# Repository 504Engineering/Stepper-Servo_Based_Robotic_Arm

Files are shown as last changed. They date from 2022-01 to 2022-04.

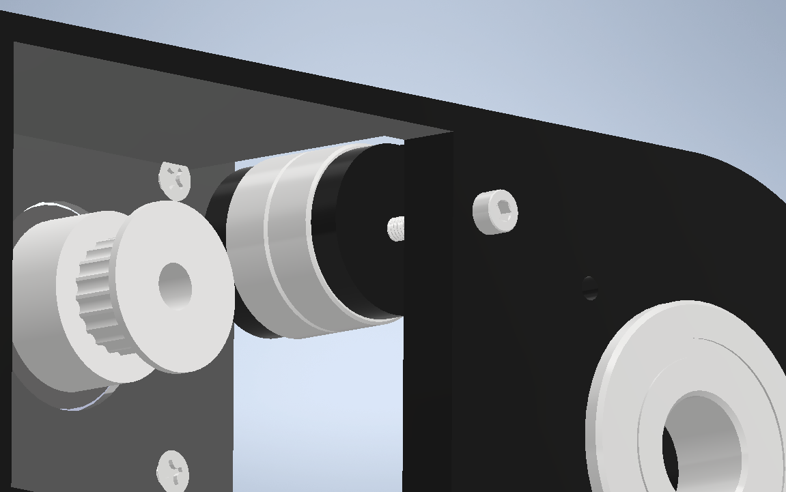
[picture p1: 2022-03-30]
Documentation/imgs/assembly6.png

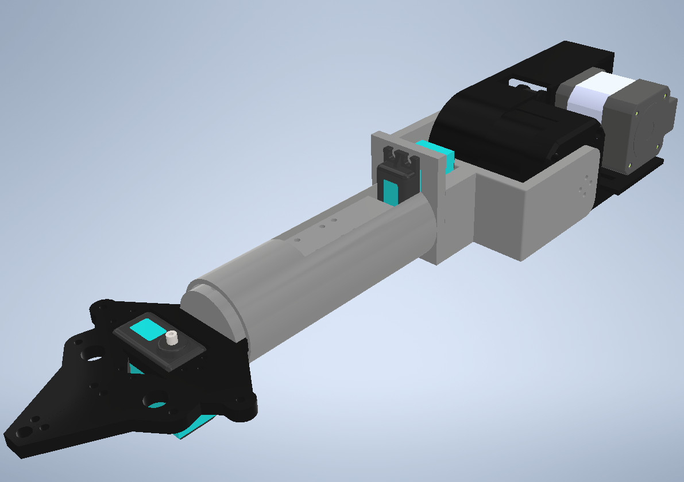
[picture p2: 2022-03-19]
Documentation/imgs/Full_Design.bmp

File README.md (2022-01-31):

# Stepper-Servo_Based_Robotic_Arm
This repository contains a robotic arm that is either a hybrid of both Servo Motors and Stepper Motors or just Stepper Motors.

Eventual completed arm will contain either four Stepper Motors or 2 Stepper Motors and 2 Servo Motors depending on which one you go with. All parts can be 3d printed and a few of the parts can be made on a cnc for quicker creation. 

At the current stage of development, the first two stages of the robotic arm's tilt are complete. 



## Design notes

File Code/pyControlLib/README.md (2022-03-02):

This Library is for use with 504 Engineering Robotic Arm. 

It is used to send signals and data to a RPI pico via a serial communication link.

Libraries that are installed with it:
    pySerial
    Numpy

This library contains useful functions that can be used to accurately store and send data to any serial device,
as long as the com port and baud rate are set correctly.

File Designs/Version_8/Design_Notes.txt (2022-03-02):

Tilt_attachment_Bracket:
	Minimum Distance in Length	97.376 mm
	Minimum Distance in Width	60 mm
	Minimim Distance in Height 	30 mm

Joint 1:
	110 mm length of gearbox = 4.331"
	Length of entire joint = 6"
	Extrusion Length = (6" - 4.331") * 25.4

	66m - 52mm = 14mm

Joint 2:
	40mm - 30mm = 10mm

twist:
	Length of rod = 65mm
	First d cut = 4 mm
	Second d cut = 65mm - 54.8mm - 4mm = 6.2mm

Claw Attachment:
	Length = 38.2mm
	Radius = max 37.5mm
	38.2 - 7e

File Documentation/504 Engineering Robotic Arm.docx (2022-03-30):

504 Engineering Robotic Arm

Documentation

By: Michael Lees

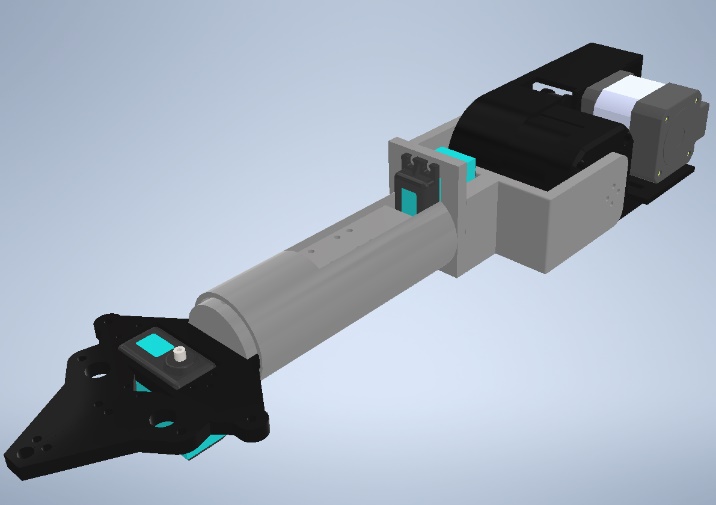
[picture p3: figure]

Table Of Contents:

- Chapter 1: Design Implementation …………………………………………………… 2
- Chapter 2: Gearbox Design …………………………………………………………... 5

Chapter 1: Design Implementation

504 Engineering’s stepper motor-based manipulator provides agile and precise movement across the ROV’s z axis. It utilizes a NEMA 17, provided by Doehler USA, which proved to be a challenge. This challenge was presented to us by North Paulding Robotics in order to achieve another first place victory in the MATE International Competition.

In December of 2021, they began the request with:

- 4-axes of movement
- At least two stepper motors in use (three if time allows)
- No servo motors in use.

They later changed the requirements, in March of 2022, to:

- 3-axes of movement
- Two stepper motors in use
- Ability to use one or two servo motors

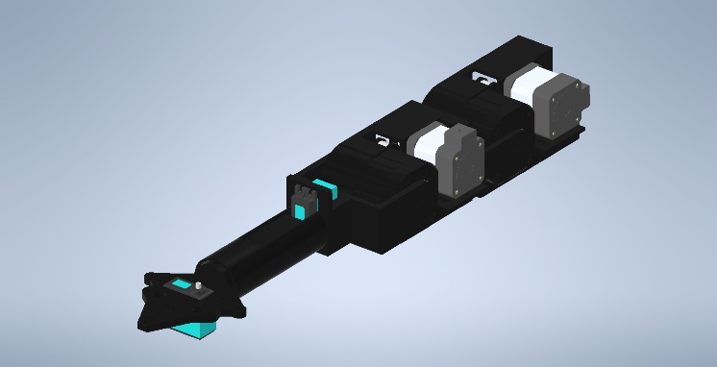
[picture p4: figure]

504 Engineering’s first design utilized four stepper motors to achieve the first set of requirements, however when inspected by North Paulding Robotics this design was determined to be an over improvement of the previous year’s design, in response a second set of requirements was given to us.

After a time period of two weeks a second design was presented, depicted in the image to the right. This design forgoes the second axis of tilt in favor of ease of use for the pilots who will not achieve the nominal amount of piloting time of the final ROV. The total time of completion of this project was four and a half months.

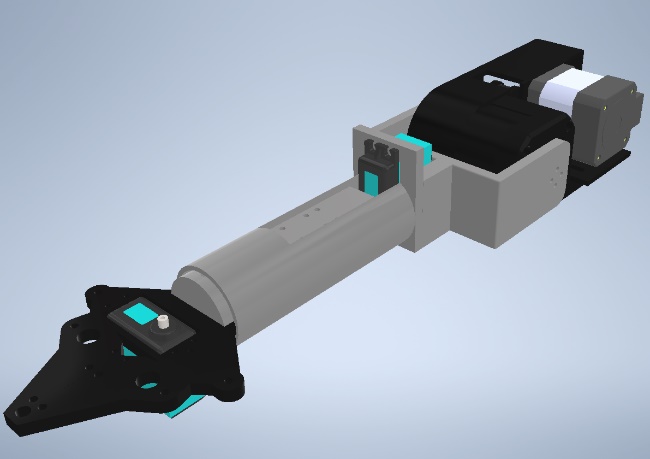
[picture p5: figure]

Chapter 2: Gearboxes

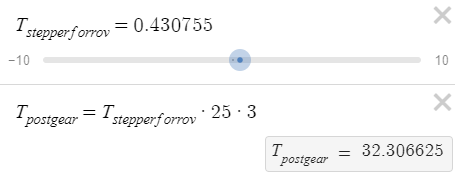
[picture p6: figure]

504 Engineering’s manipulator contains a NEMA 17 stepper motor with a holding torque capacity of 0.43 Newton-meter. This holding torque capacity, during initial testing, was determined to be inadequate for North Paulding Robotics needs. Testing proved that the utilization of a speed reducer gearbox provided the needed results to prove useful. With the utilization of a v-belt system (gear ratio of 3:1) along with the dual speed reduction gearbox, which was a 25:1 gear ratio, the holding torque of the NEMA 17 was increased to 32.31 Newton-meters.

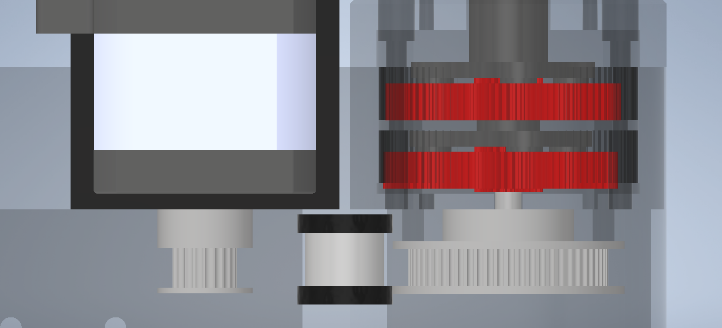
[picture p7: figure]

This combination of the v-belt system (the silver portions of the picture below) and the speed reduction gearbox (red portions) allowed for a 75:1 gear reduction of the NEMA 17. While this improved the overall torque capacity of the motor, it lessened the speed of the overall tilt. However, after research into the team’s previous manipulator designs it was shown that the angular speed of the tilt body was only slightly slower than the servo-based design used previously. Further research into the newly designed manipulator showed that the overall lifting capacity of the newly designed tilt was 9.08 kilograms at the overall length of the manipulator.

As you can see to the right, at the distance of 0.3 meter, the newly designed manipulator achieves a lifting force of 120.02 Newtons and a weight capacity of 12.25 kilograms. Included in the image is the calculations performed with the stepper motor without any gear reductions or v-belt systems, it can only achieve a lifting force of 1.6 Newtons and a weight capacity of 0.163 kilograms.

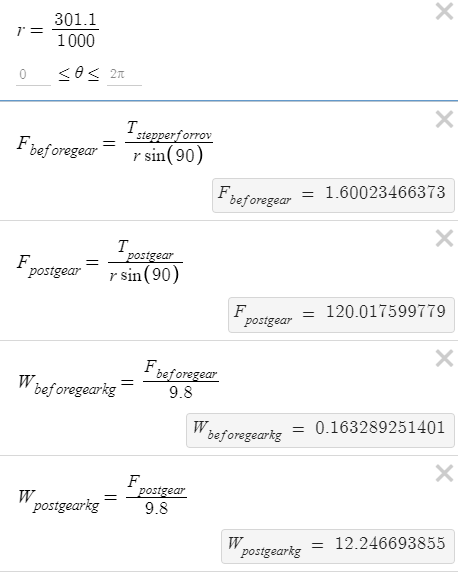
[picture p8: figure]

During the testing phases of the development of this gearbox reduction system, 504 Engineering tested various other options as well. Such as a cycloidal drive system, a harmonic drive system, stand-alone speed reduction gearboxes, and stand-alone v-belt systems. None of the listed options provided the nominal weight capacity required for the MATE International Competition as listed in their Product Demonstration Manual.

Chapter 3:

Part codex | Location in Parts Box | Description | Image

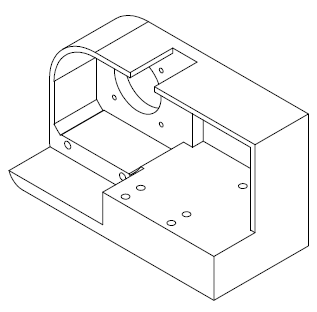
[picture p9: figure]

A0000 | | The base of tilt system

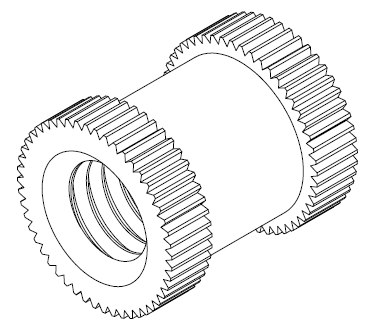
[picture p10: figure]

A0001 | | Threaded inserts

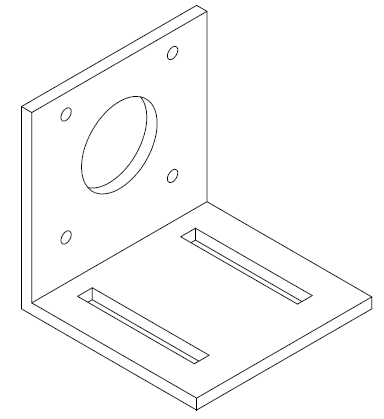
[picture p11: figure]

A0002 | | Black mount plate provided in the spare parts toolbox.

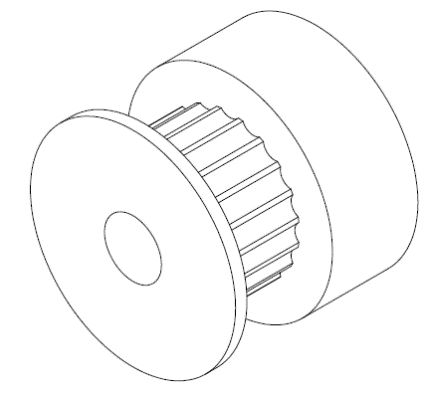
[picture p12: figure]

A0003 | | GT2 20 Tooth Drive Pulley
A0004 | | NEMA 17 Part number: STP-MTR-17040W Provided by: Doehler USA
A0005 | | Tension Bearing Holder Part 1

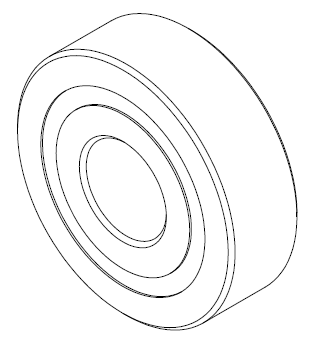
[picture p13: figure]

A0006 | | Tension Bearing, 626-2RS
A0007 | | Tension Bearing Holder Part 2

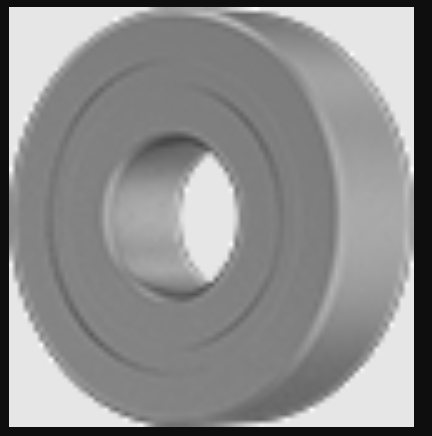
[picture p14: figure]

A0008 | | Side of Tilt Bearing 6021-2Z

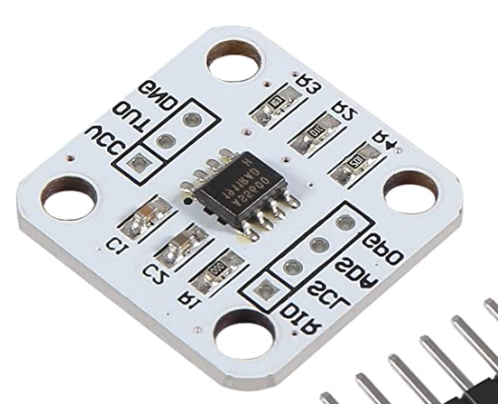
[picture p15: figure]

A0009 | | Magnetic Encoder

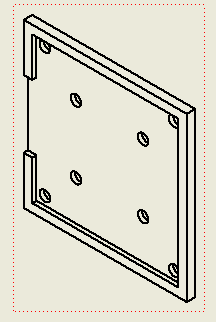
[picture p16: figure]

A0010 | | Magnetic Encoder Mounting Plate

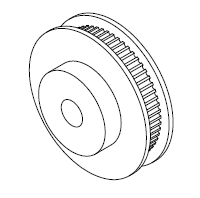
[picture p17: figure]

A0011 | | GT2 60 Tooth Belt Pulley
A0012 | | 5 mm x 30mm Aluminum Rod with a D slotted end

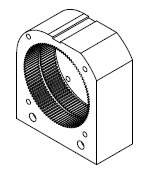
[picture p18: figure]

A0013 | | Speed Reducing Gear Box Casing
A0014 | | Sun Gear

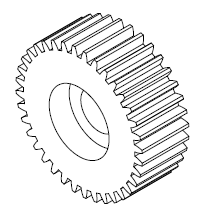
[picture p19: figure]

A0015 | | Planet Gear

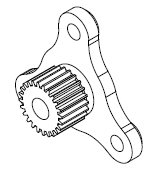
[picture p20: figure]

A0016 | | Planet Gear Output Bracket
A0017 | | Speed Reducing Gear box Output Shaft

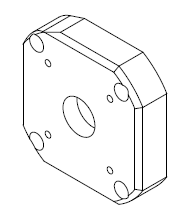
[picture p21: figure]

A0018 | | Speed Reducing Gearbox Casing Lid
A0019 | | Magnet
A0020 | | Tilt to Twist Bracket

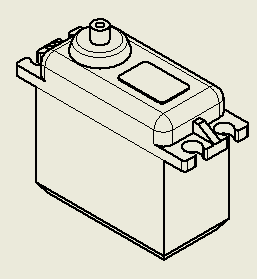
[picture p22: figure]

A0021 | | Savox Servo

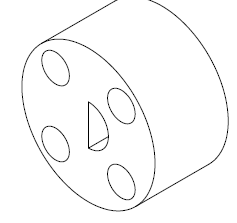
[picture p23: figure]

A0022 | | Servo To Twist Rod Attachment

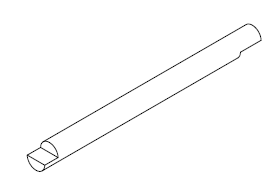
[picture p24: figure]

A0023 | | 5mm x 65mm Aluminum Rod for Twist Attachment

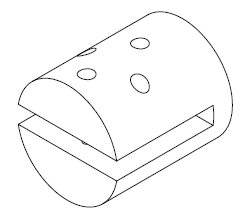
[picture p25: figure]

A0024 | | Claw Attachment

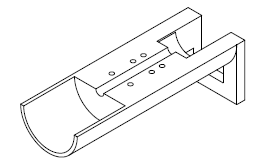
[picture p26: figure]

A0025 | | Twist Body Rod

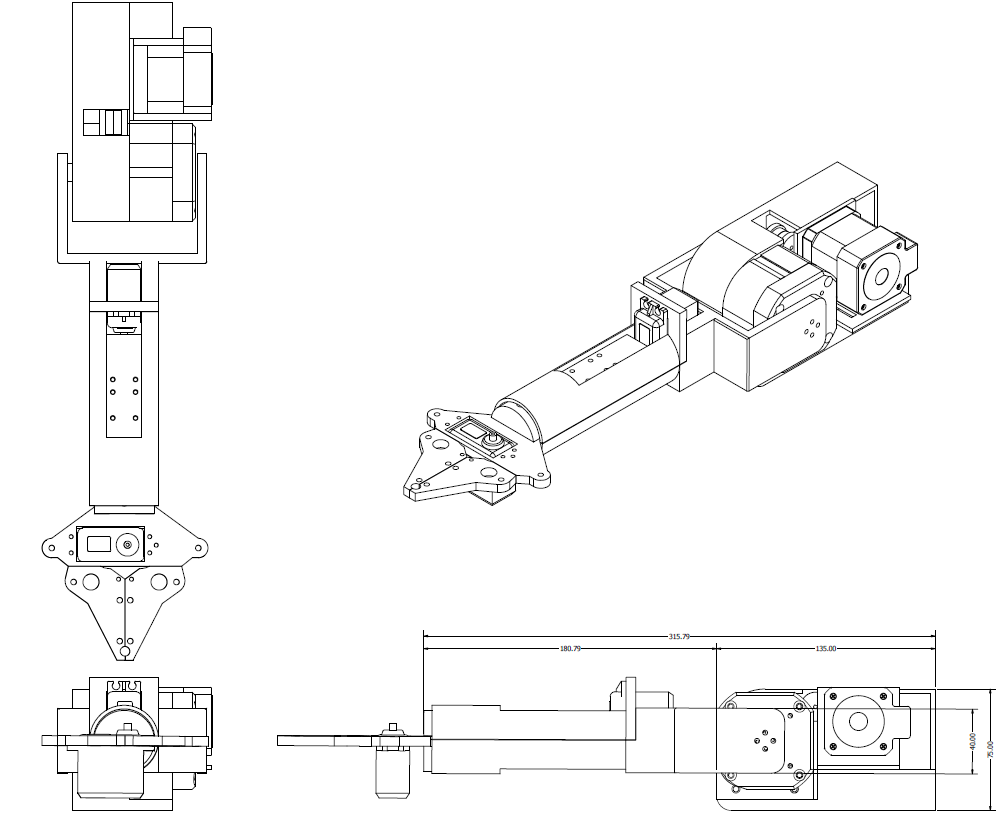
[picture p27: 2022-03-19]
Documentation/imgs/Full_Design.png

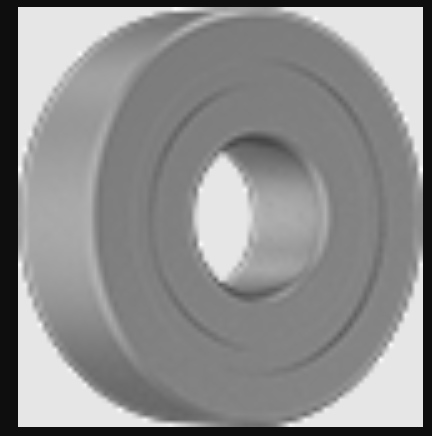
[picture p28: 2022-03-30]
Documentation/imgs/A0008.png

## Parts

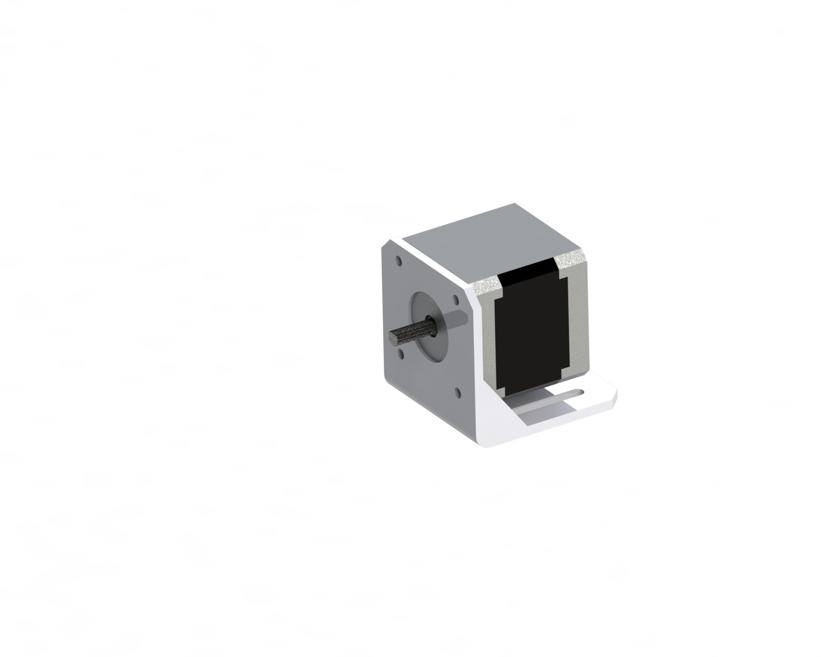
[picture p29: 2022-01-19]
Designs/Versions1-3/Downloaded Parts/nema-17-motor-mount-1.snapshot.1/Nema 17 motor mount.png

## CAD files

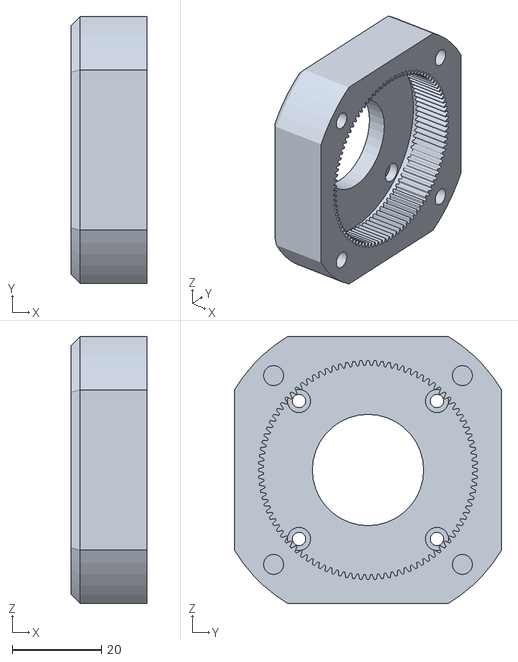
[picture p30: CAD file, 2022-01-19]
Designs/Version_8/Downloaded_Parts/nema17-speed-reducer-1.snapshot.9/STL/96_Teeth_Gear.stl
17.0 x 60.0 x 60.0

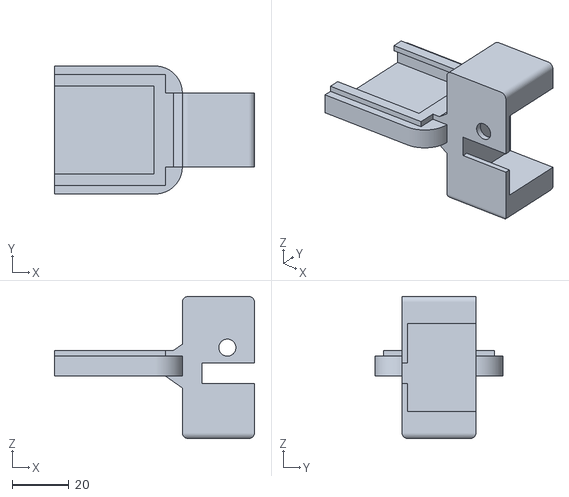
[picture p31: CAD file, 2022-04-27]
Designs/Version_8/Exported_Parts/stl/Tilt_Camera_Servo_Mount.stl
70.4 x 45.0 x 50.0

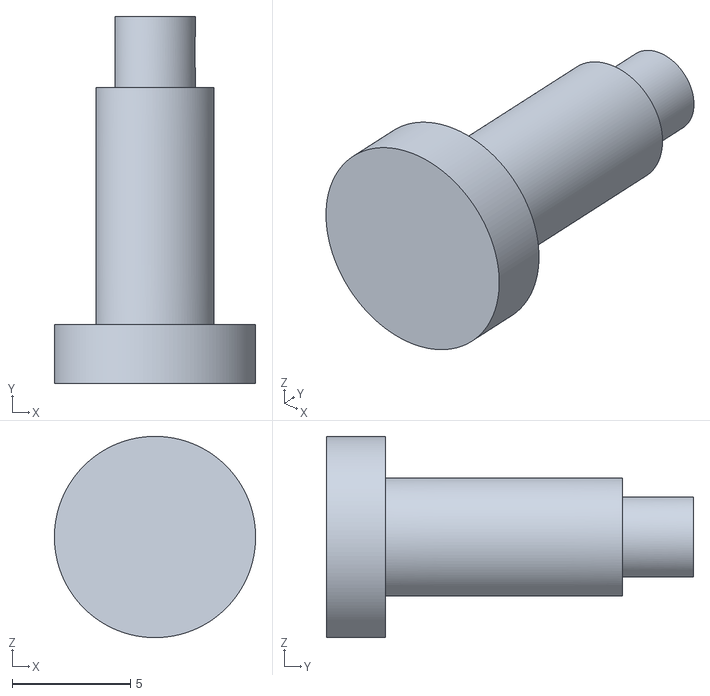
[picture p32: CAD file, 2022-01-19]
Designs/Versions1-3/Created Parts/Gear_Attachment.stl
8.50 x 15.5 x 8.50

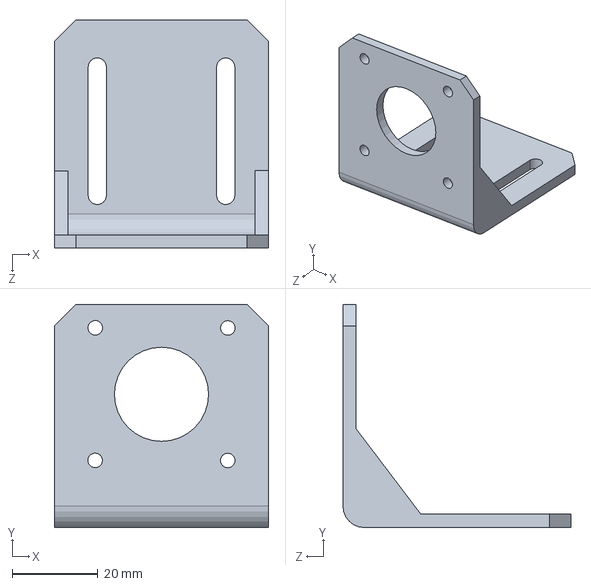
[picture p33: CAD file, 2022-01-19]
Designs/Versions1-3/Downloaded Parts/nema-17-motor-mount-1.snapshot.1/NEMA_17_Bracket.SLDPRT
50.0 x 52.1 x 53.3 mm

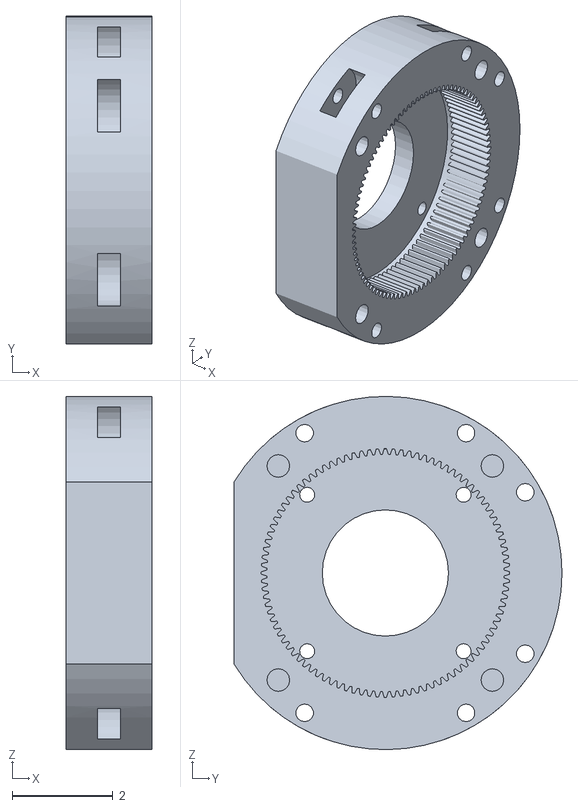
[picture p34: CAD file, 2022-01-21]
Designs/Versions1-3/stl/96_Teeth_Gear.step_modified_bearings.stl
1.70 x 6.50 x 7.00

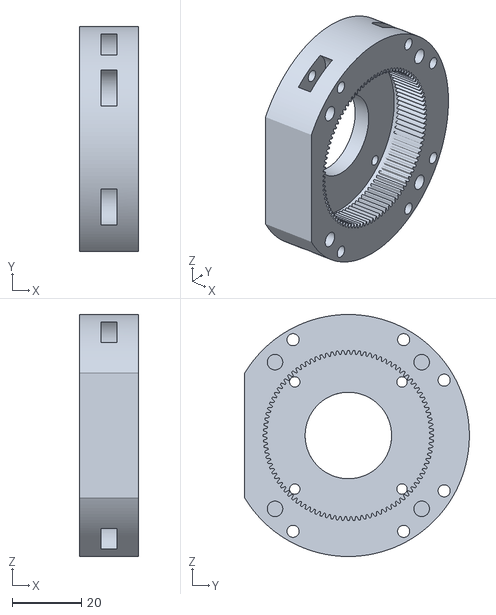
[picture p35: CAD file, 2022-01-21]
Designs/Versions1-3/stl/rev_3/96_Teeth_Gear.step_modified_bearings.stl
17.0 x 65.0 x 70.0

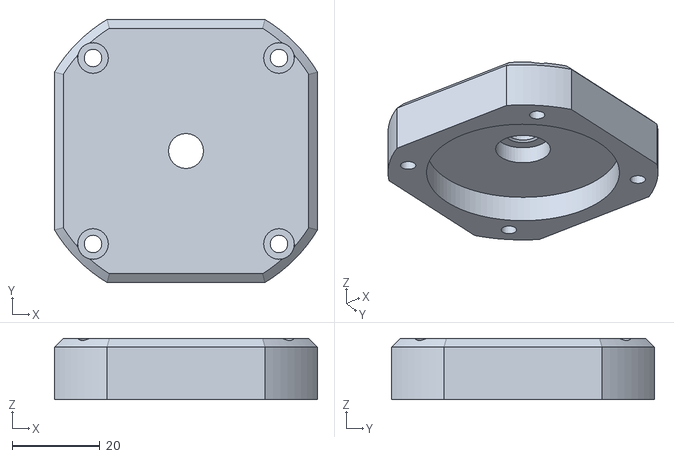
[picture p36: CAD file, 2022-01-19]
Designs/Version_8/Downloaded_Parts/nema17-speed-reducer-1.snapshot.9/STL/Gear_Cover.stl
60.0 x 60.0 x 14.0

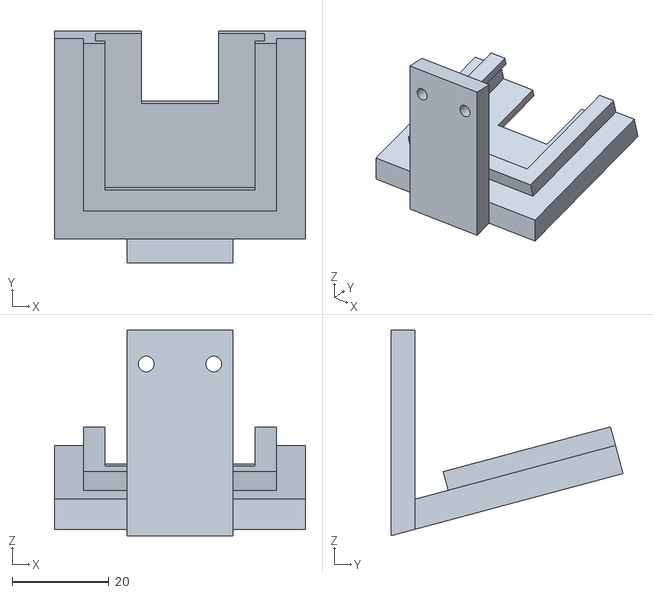
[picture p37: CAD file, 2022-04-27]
Designs/Version_8/Exported_Parts/stl/Camera_Mount.stl
52.0 x 48.1 x 42.6

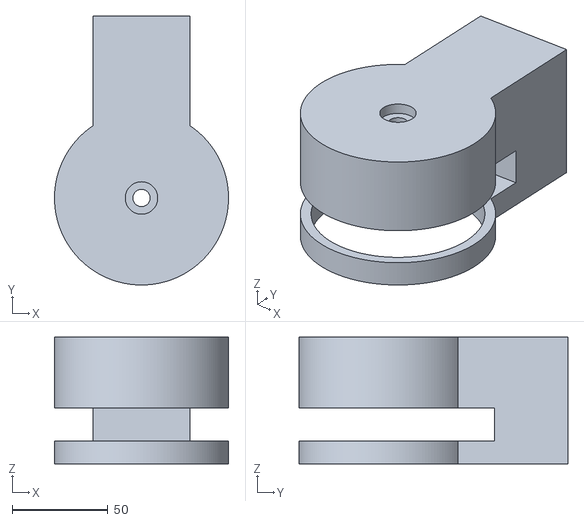
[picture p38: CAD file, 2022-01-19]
Designs/Versions1-3/Created Parts/Tilt_Portion.stl
91.0 x 140.6 x 66.2

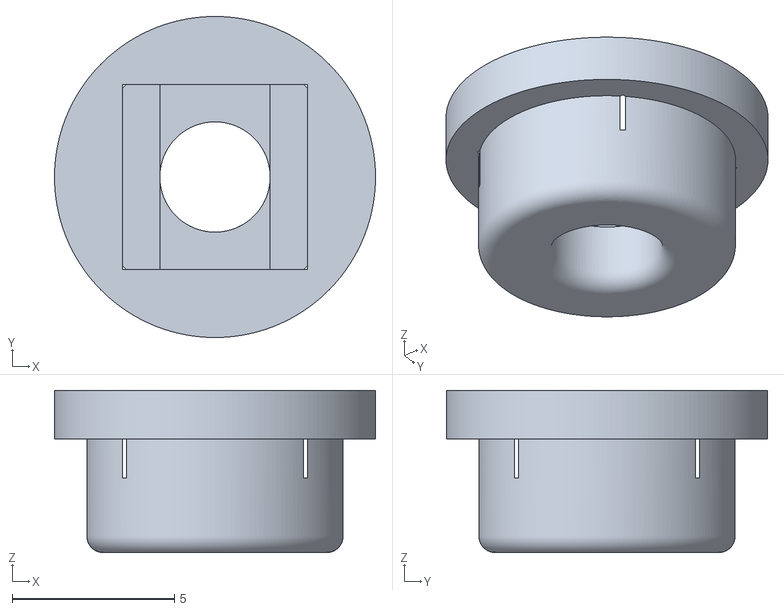
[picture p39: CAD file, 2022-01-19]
Designs/Versions1-3/stl/HD_BearingShaft1.stl
9.90 x 9.90 x 5.00

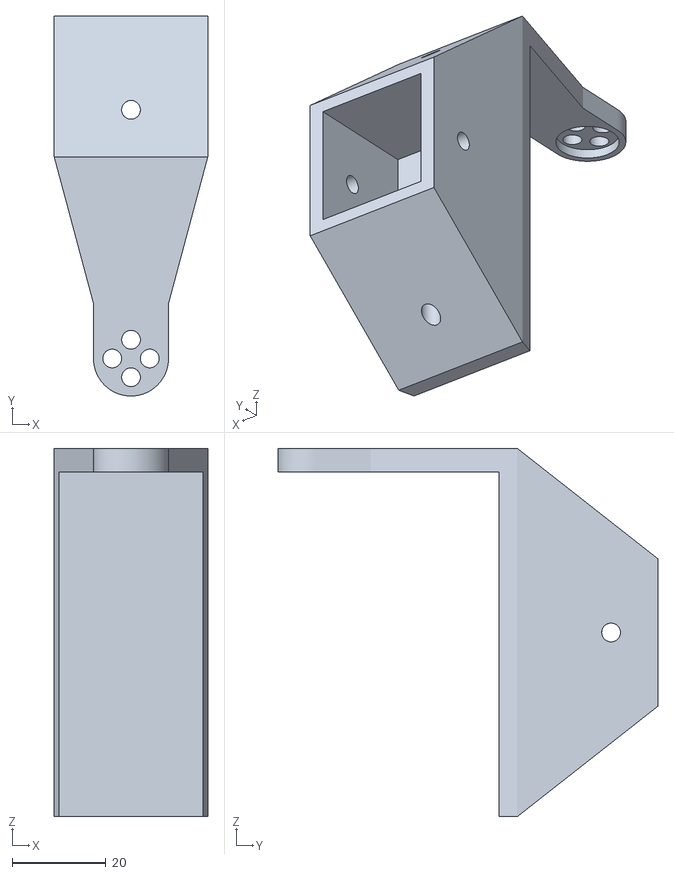
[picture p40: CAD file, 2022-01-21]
Designs/Versions1-3/stl/rev_3/OutPut_Shaft_From_Gearbox.stl
32.8 x 81.0 x 78.5

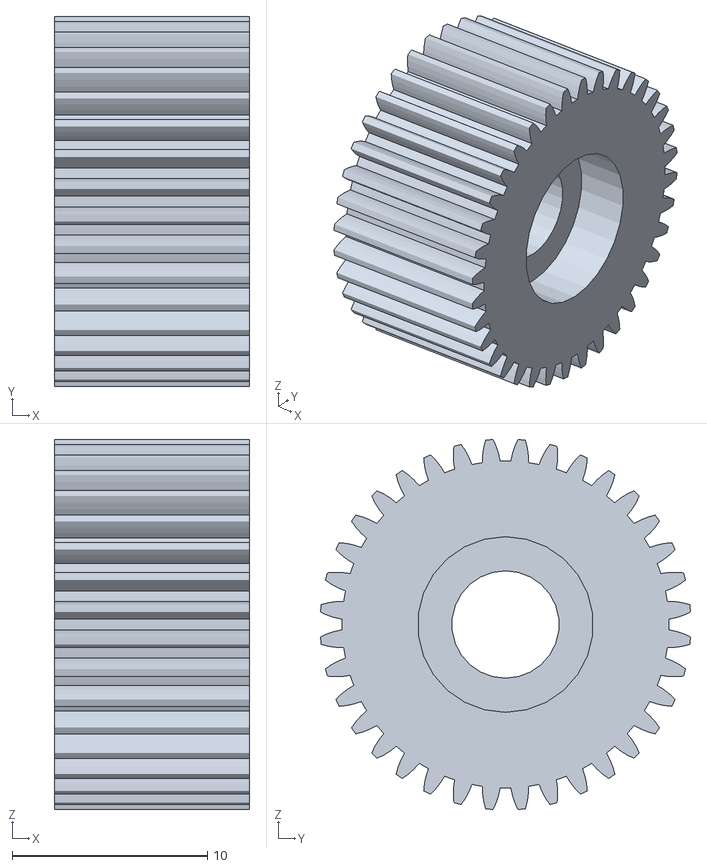
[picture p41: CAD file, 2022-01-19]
Designs/Version_8/Downloaded_Parts/nema17-speed-reducer-1.snapshot.9/STL/36_Teeth_Planet_Gear.stl
10.0 x 19.0 x 19.0

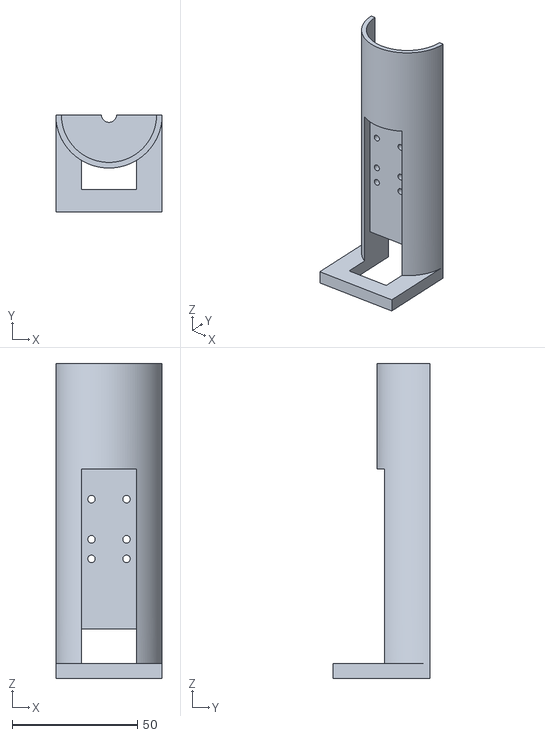
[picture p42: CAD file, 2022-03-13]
Designs/Version_8/Exported_Parts/stl/Tilt_Bracket_Output_2_Lid.stl
42.5 x 38.9 x 125.8

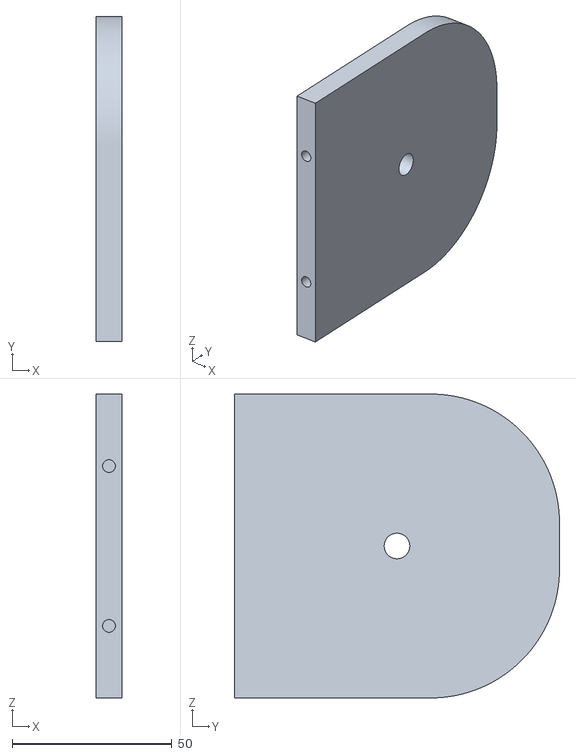
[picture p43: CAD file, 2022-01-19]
Designs/Versions1-3/Created Parts/Base_Attachment.stl
8.00 x 101.6 x 95.0

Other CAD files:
Designs/Version_8/Design_Sheets/Full_Design.dwg
Designs/Version_8/Design_Sheets/Mag_Shield_Back.dwg
Designs/Version_8/Design_Sheets/ServoSW-1211SG.dwg
Designs/Versions1-3/stl/Gear_Cover_modified.stl
Designs/Documentation_assembly/Assembly1.iam
Designs/Documentation_assembly/OldVersions/Assembly1.0002.iam
Designs/Version_4/Created_Parts/24_Teeth_Sun_Gear.ipt
Designs/Version_4/Created_Parts/36_Teeth_Planet_Gear.ipt
Designs/Version_4/Created_Parts/Bearing_mark_up.ipt
Designs/Version_4/Created_Parts/Gear_Cover_modified.ipt
Designs/Version_4/Created_Parts/Metal_Bone.ipt
Designs/Version_4/Created_Parts/Metal_Shroud_tilt_1.ipt
Designs/Version_4/Created_Parts/Motor_Mount.ipt
Designs/Version_4/Created_Parts/Motor_Mount_Backplate.ipt
Designs/Version_4/Created_Parts/Nema17.ipt
Designs/Version_4/Created_Parts/OldVersions/24_Teeth_Sun_Gear.0002.ipt
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

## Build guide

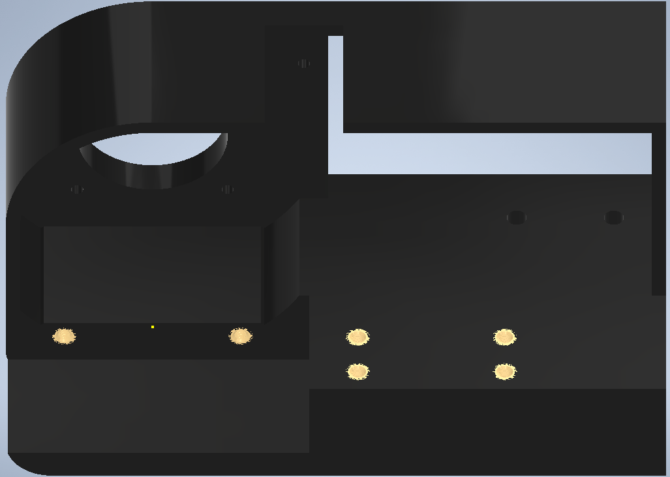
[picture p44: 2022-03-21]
Documentation/imgs/assembly0.png

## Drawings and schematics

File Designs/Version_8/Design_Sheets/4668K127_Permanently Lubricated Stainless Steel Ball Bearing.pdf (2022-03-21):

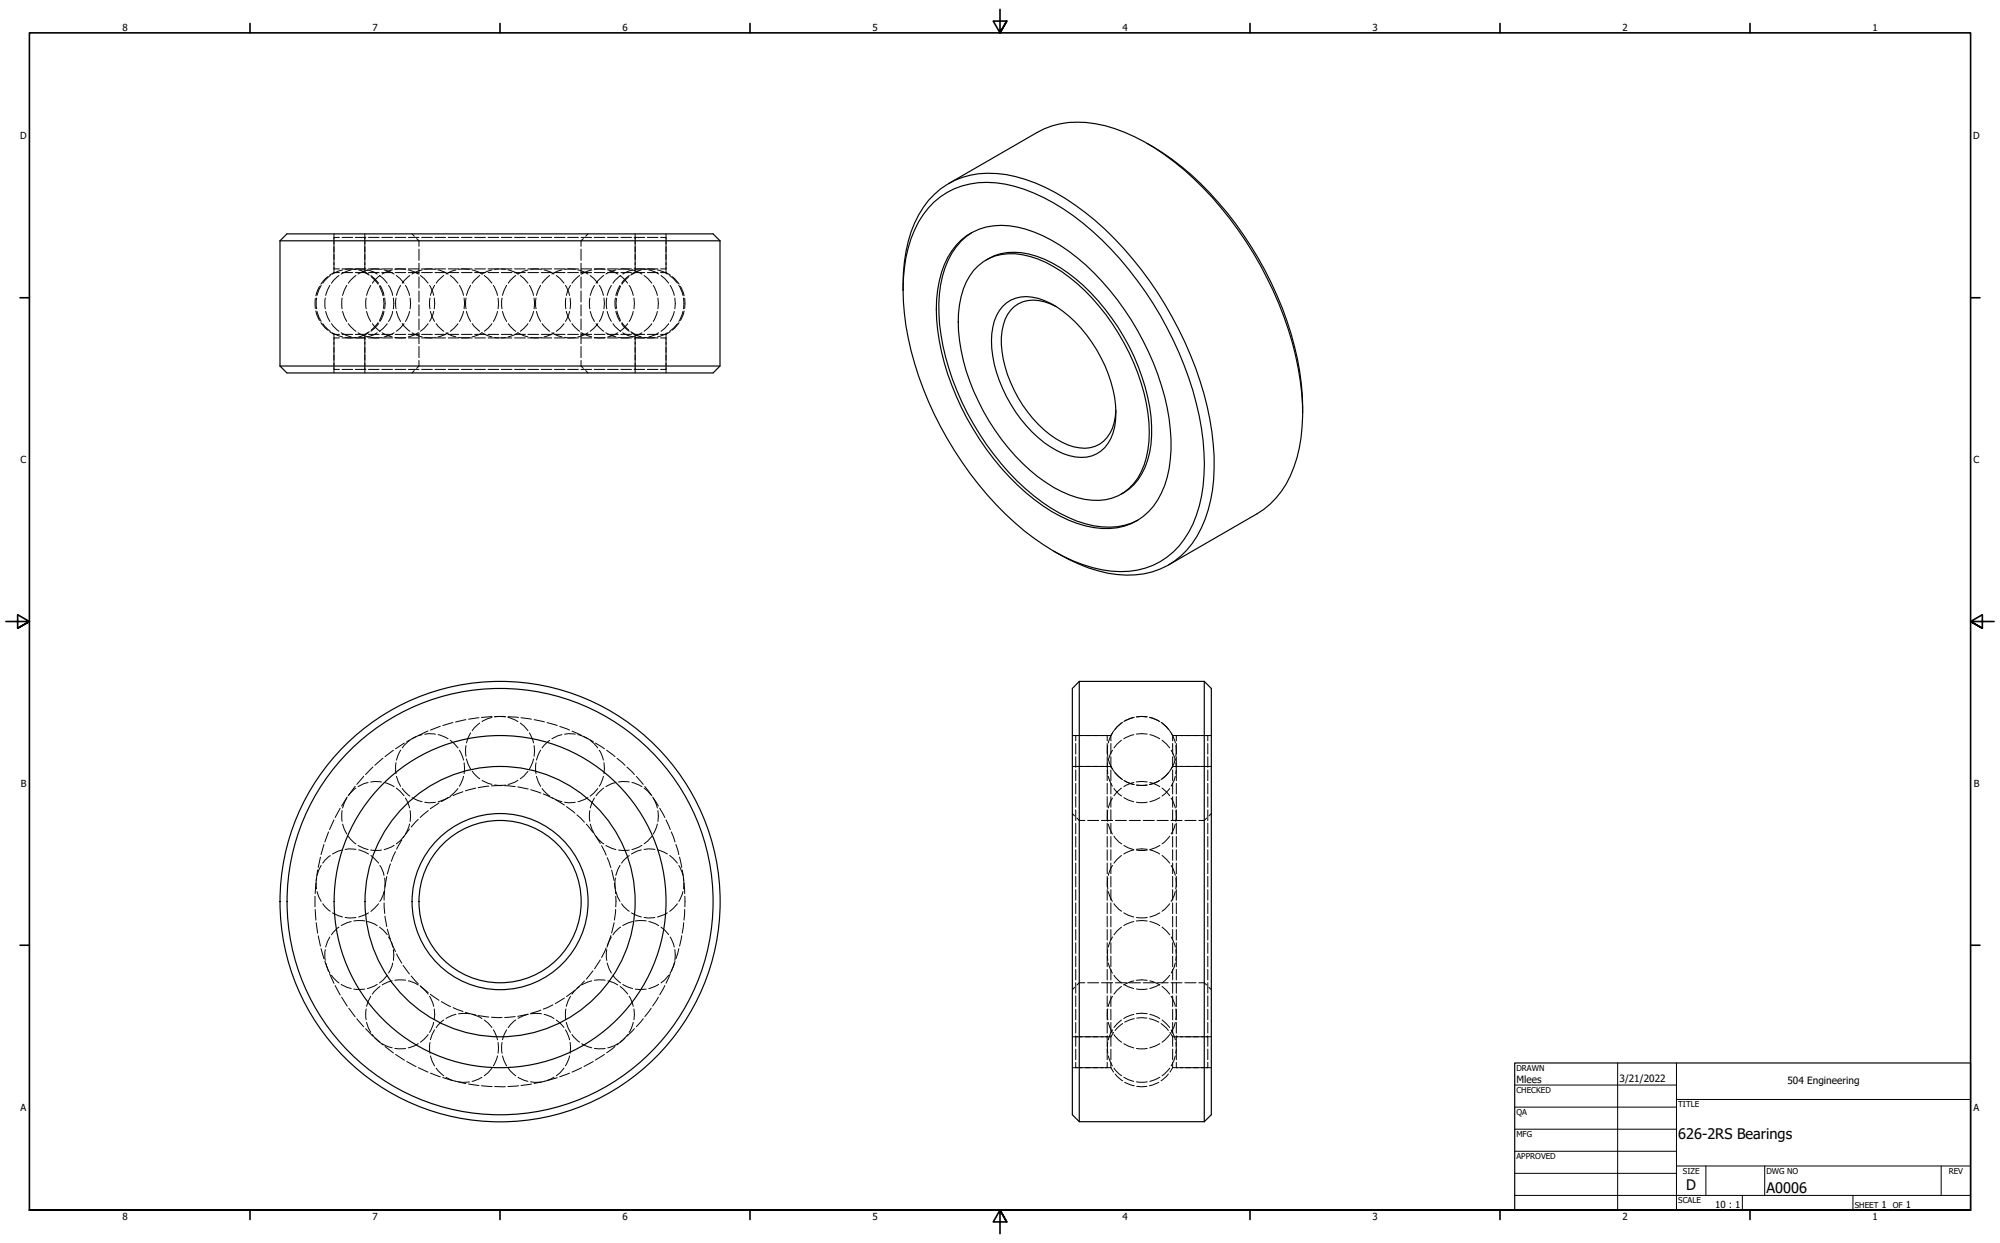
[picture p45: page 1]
626-2RS Bearings

DRAWN Mlees | 3/21/2022 | 504 Engineering

CHECKED

MFG

APPROVED

SIZE D | DWG NO A0006 | REV

SCALE 10 : 1 | | SHEET 1 OF 1

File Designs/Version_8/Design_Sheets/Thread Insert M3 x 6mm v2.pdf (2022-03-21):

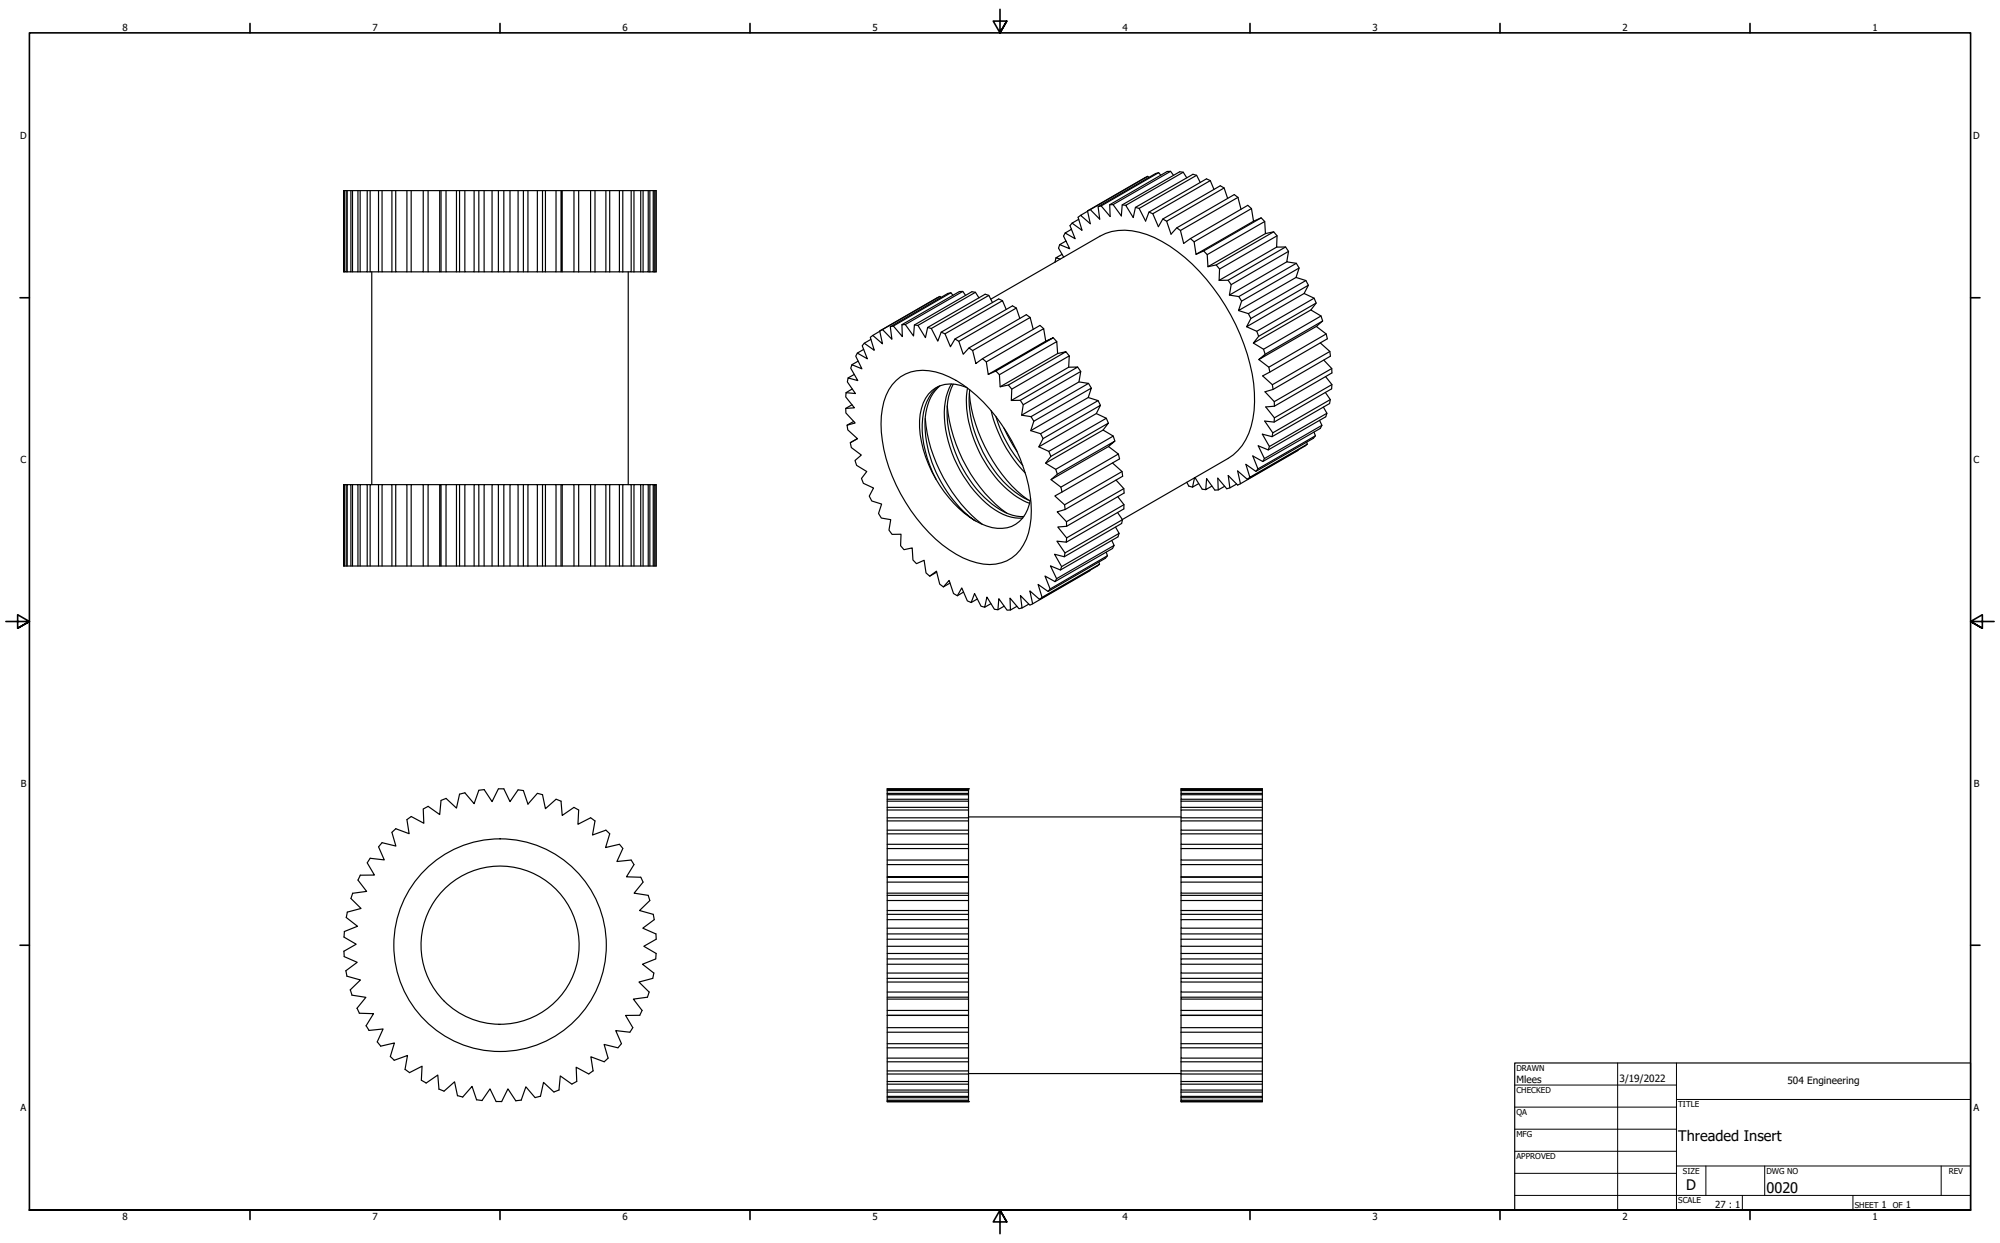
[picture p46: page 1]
Threaded Insert

DRAWN Mlees | 3/19/2022 | 504 Engineering

CHECKED

MFG

APPROVED

SIZE D | DWG NO 0020 | REV

SCALE 27 : 1 | | SHEET 1 OF 1

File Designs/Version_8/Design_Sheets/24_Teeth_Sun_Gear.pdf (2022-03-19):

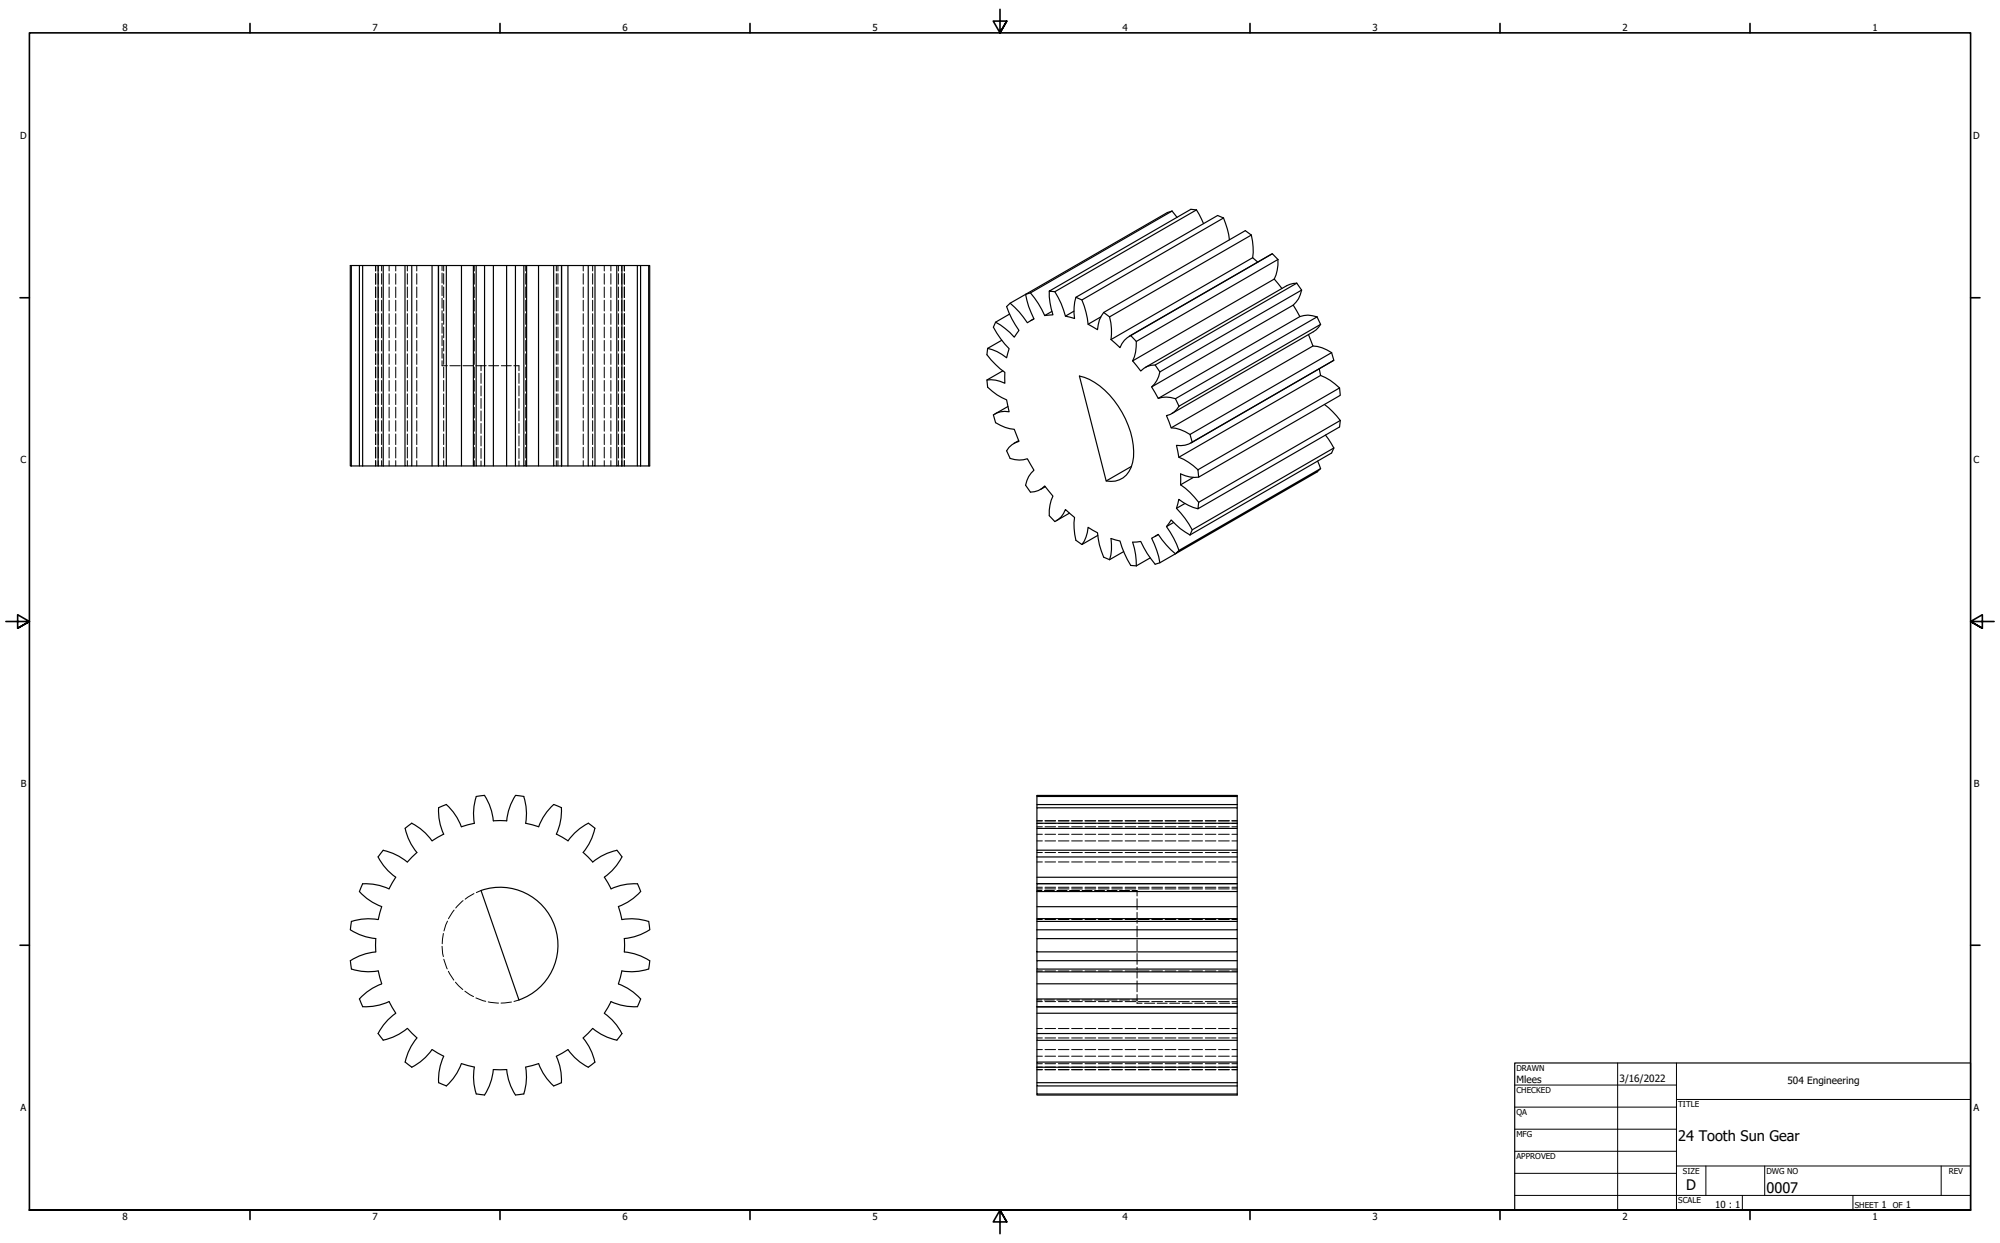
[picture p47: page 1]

DRAWN Mlees | 3/16/2022 | 504 Engineering

CHECKED

MFG

24 Tooth Sun Gear

APPROVED

SIZE D | DWG NO 0007 | REV

SCALE 10 : 1 | | SHEET 1 OF 1

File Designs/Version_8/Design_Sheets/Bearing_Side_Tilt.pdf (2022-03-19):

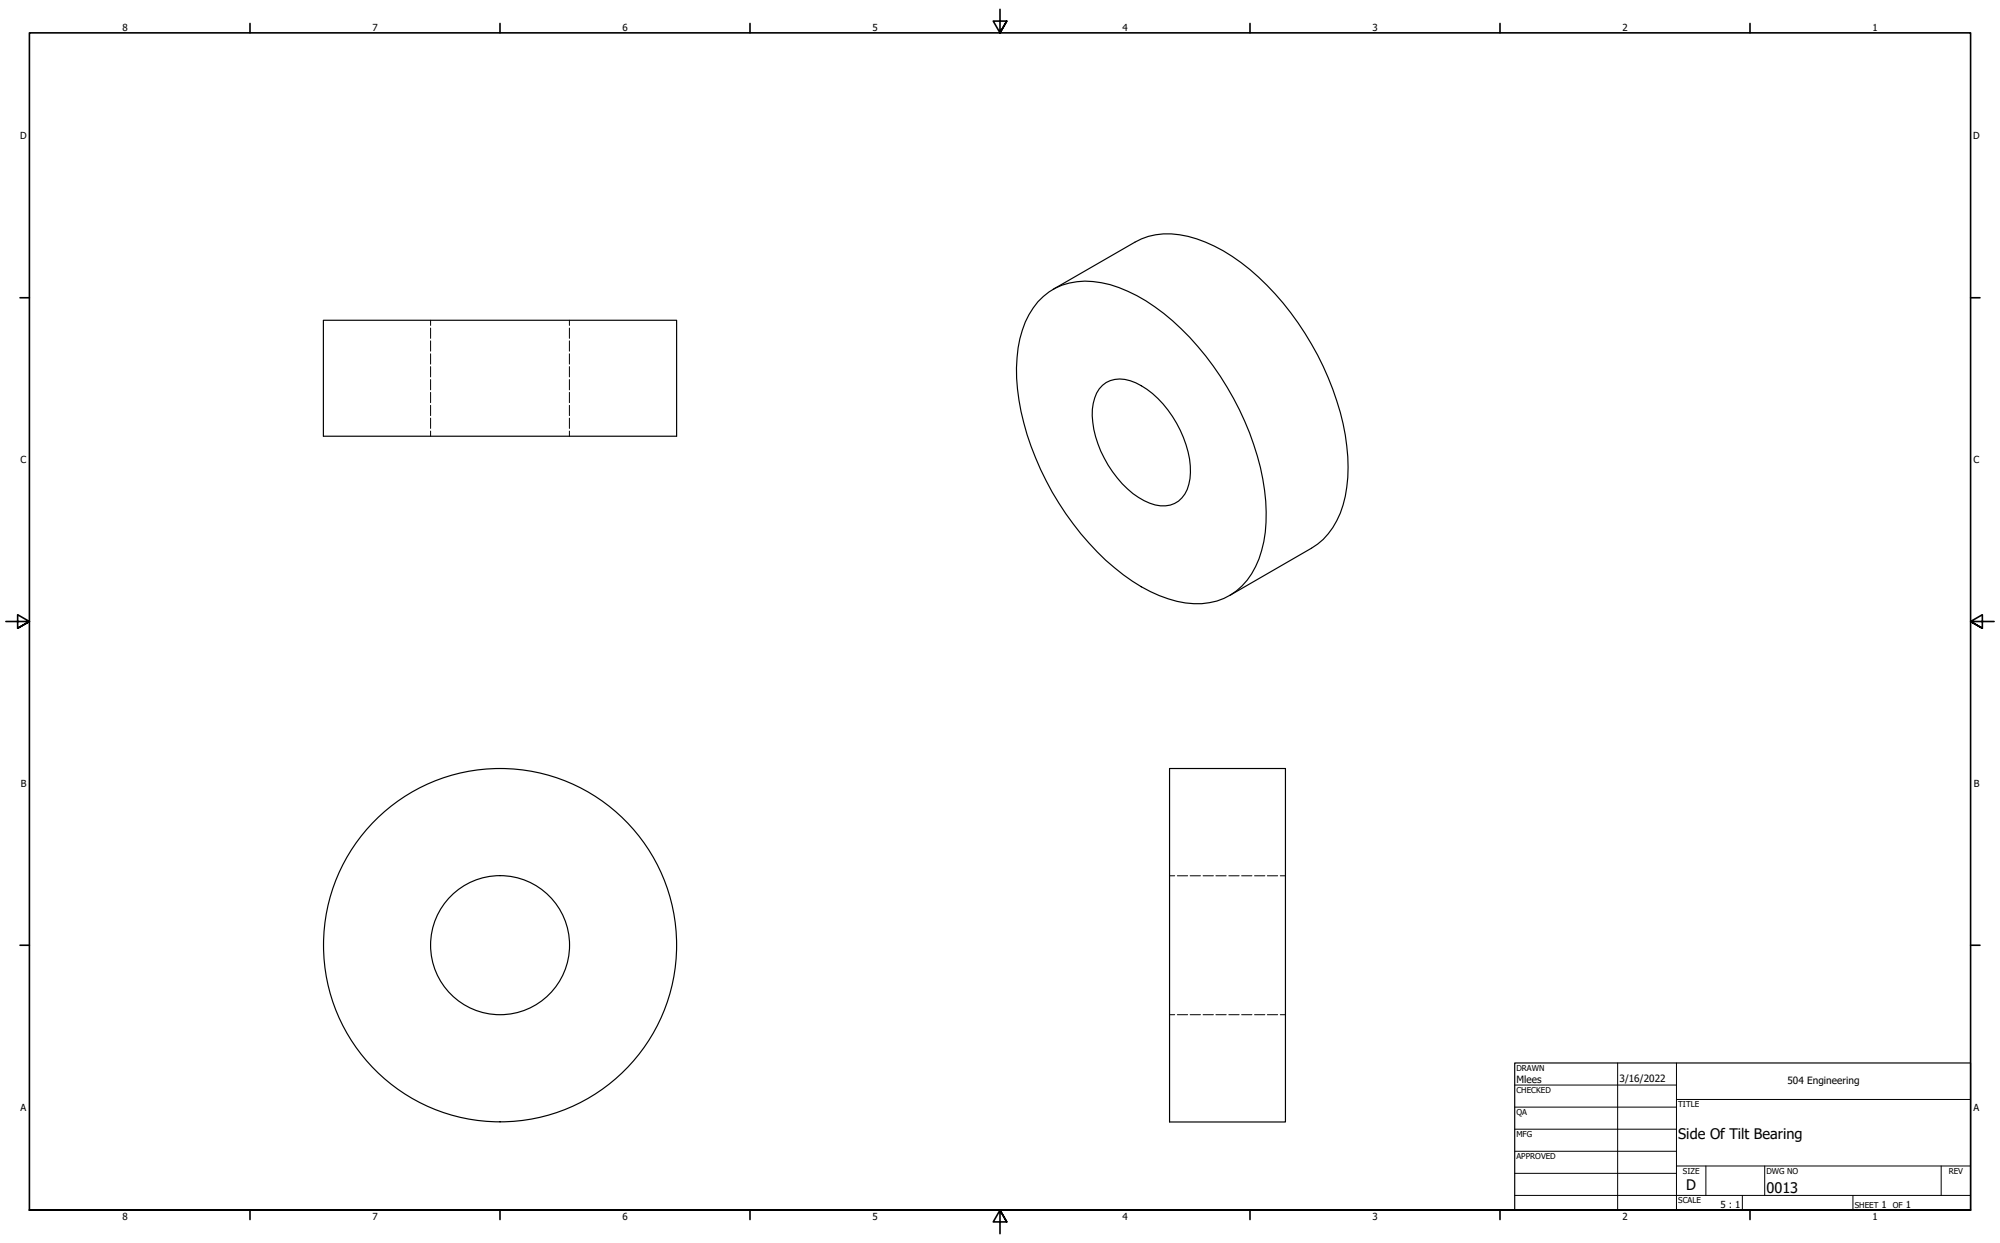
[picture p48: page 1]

DRAWN Mlees | 3/16/2022 | 504 Engineering

CHECKED

Side Of Tilt Bearing

MFG

APPROVED

SIZE D | DWG NO 0013 | REV

SCALE 5 : 1 | | SHEET 1 OF 1

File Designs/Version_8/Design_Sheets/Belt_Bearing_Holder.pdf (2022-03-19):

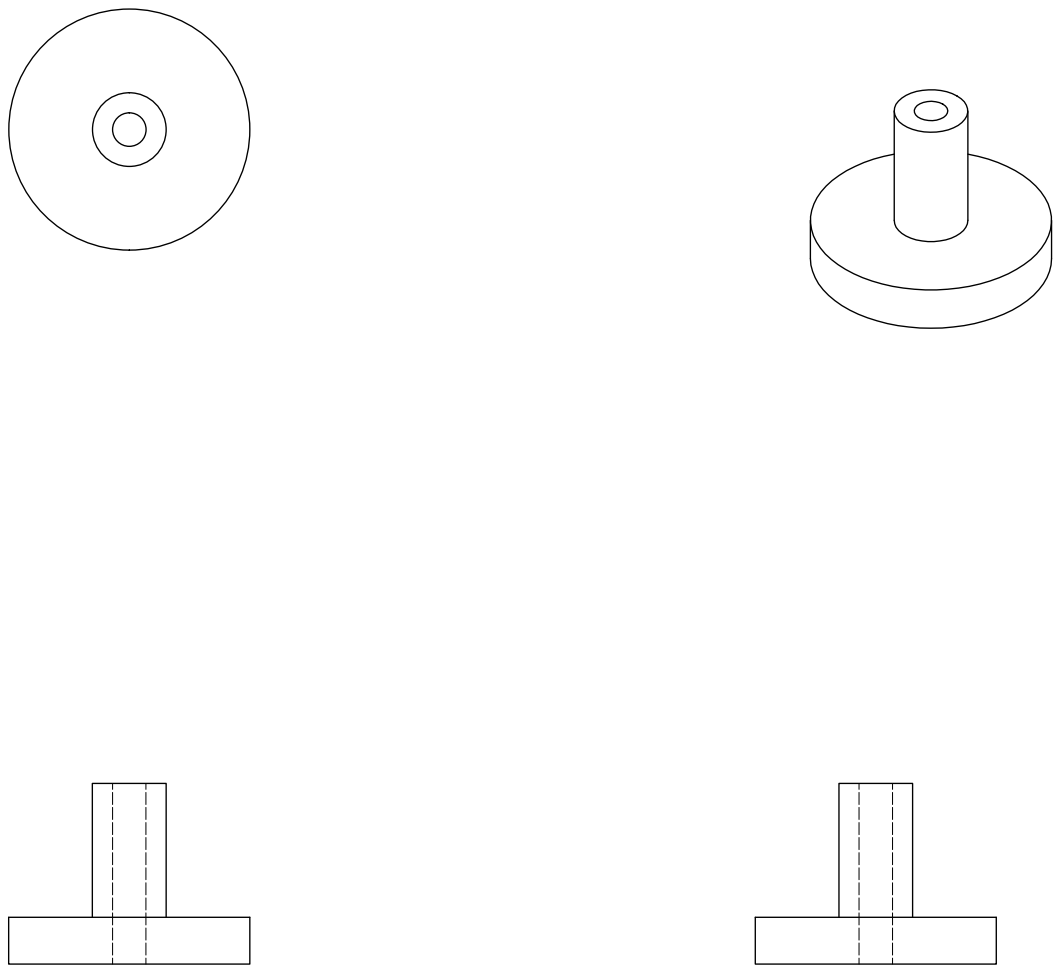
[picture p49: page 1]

DRAWN Mlees | 3/16/2022 | 504 Engineering

CHECKED

TITLE
Tension Bearing Holder

MFG

APPROVED

SIZE D | DWG NO 0012.1 | REV

SCALE 5 : 1 | | SHEET 1 OF 1

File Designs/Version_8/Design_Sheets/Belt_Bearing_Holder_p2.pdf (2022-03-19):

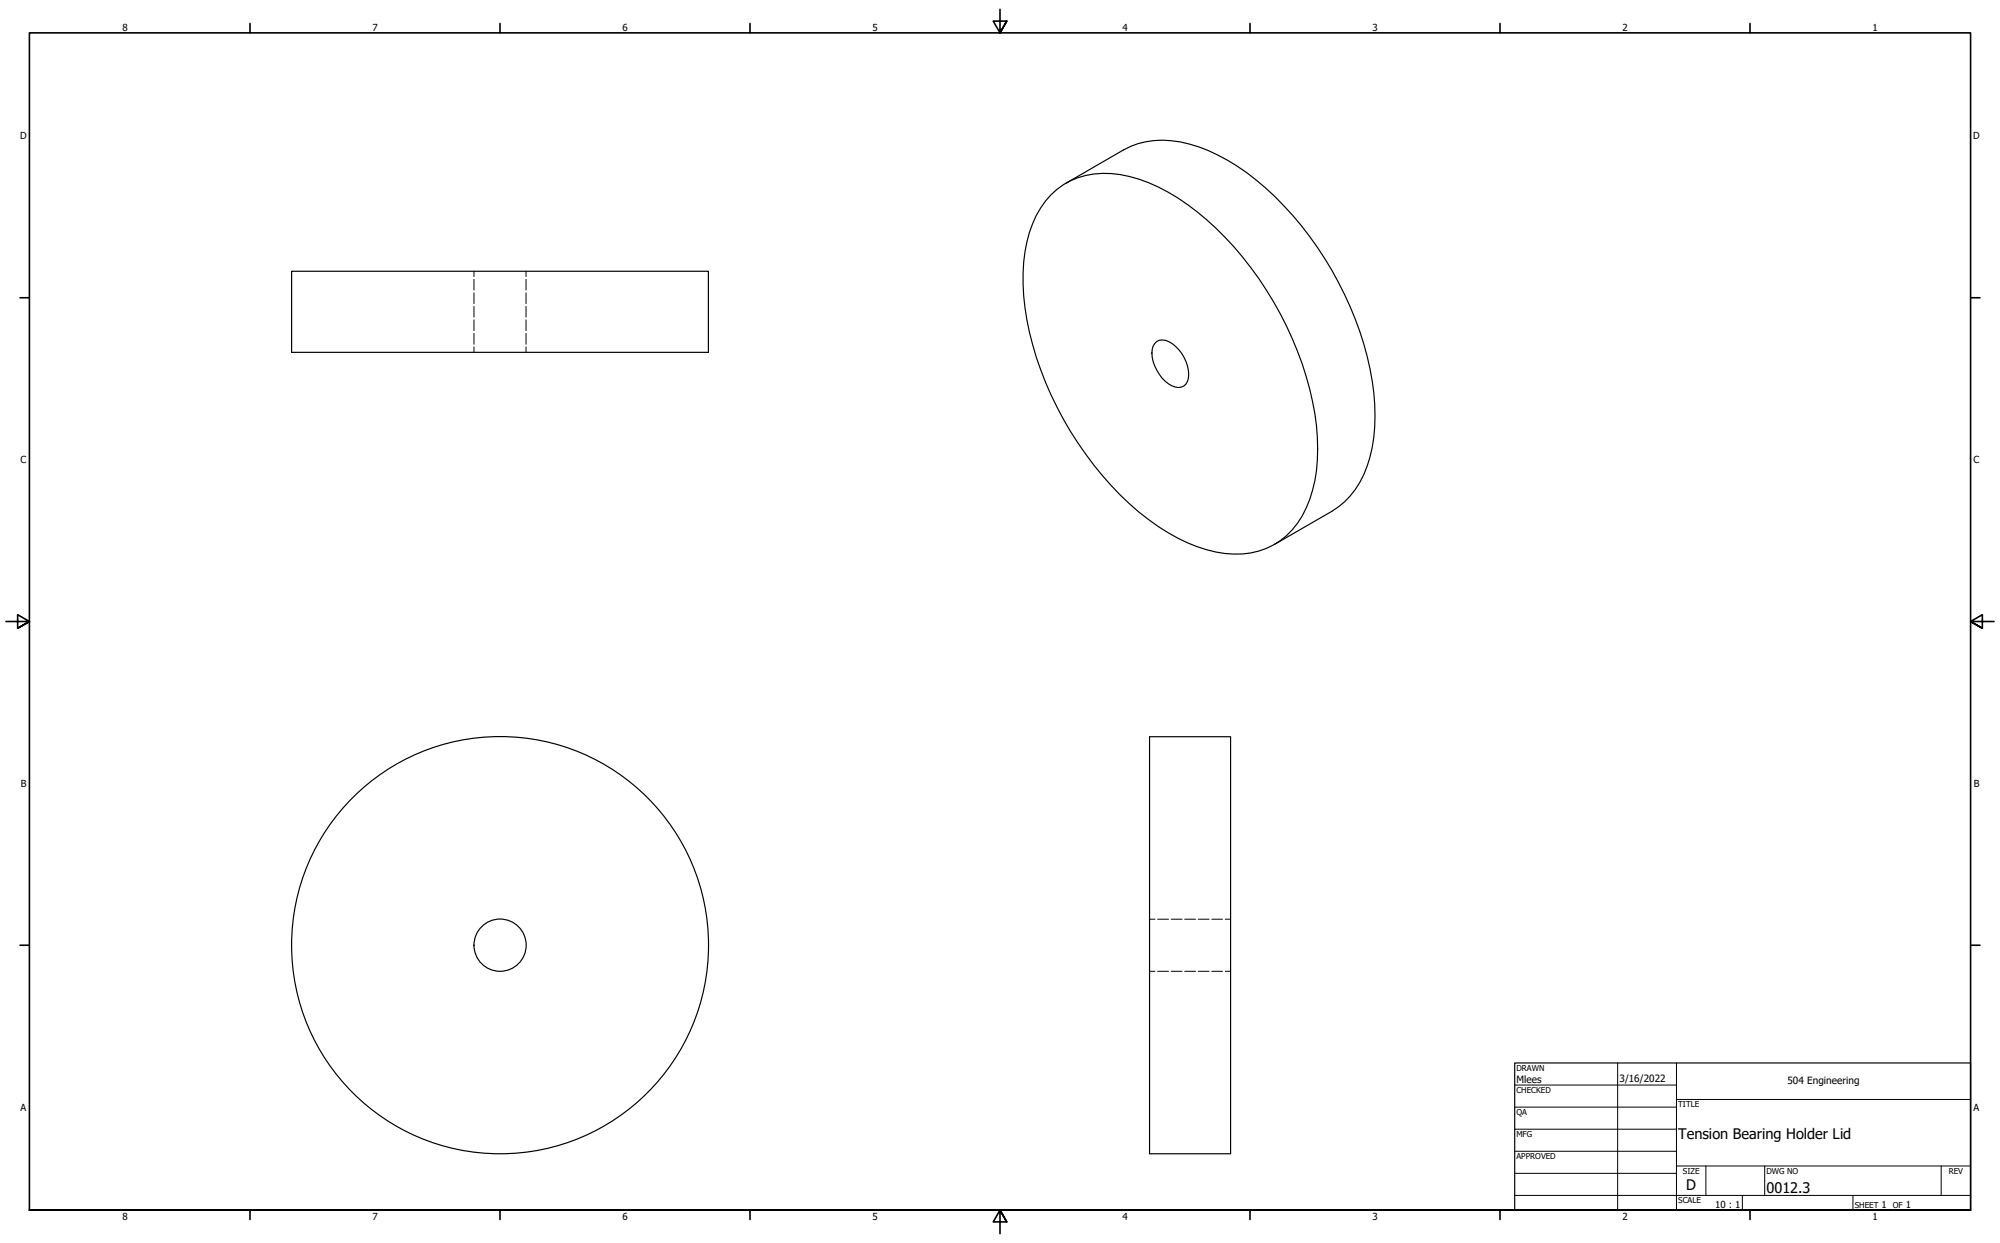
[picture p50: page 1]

DRAWN Mlees | 3/16/2022 | 504 Engineering

CHECKED

TITLE
Tension Bearing Holder Lid

MFG

APPROVED

SIZE D | DWG NO 0012.3 | REV

SCALE 10 : 1 | | SHEET 1 OF 1

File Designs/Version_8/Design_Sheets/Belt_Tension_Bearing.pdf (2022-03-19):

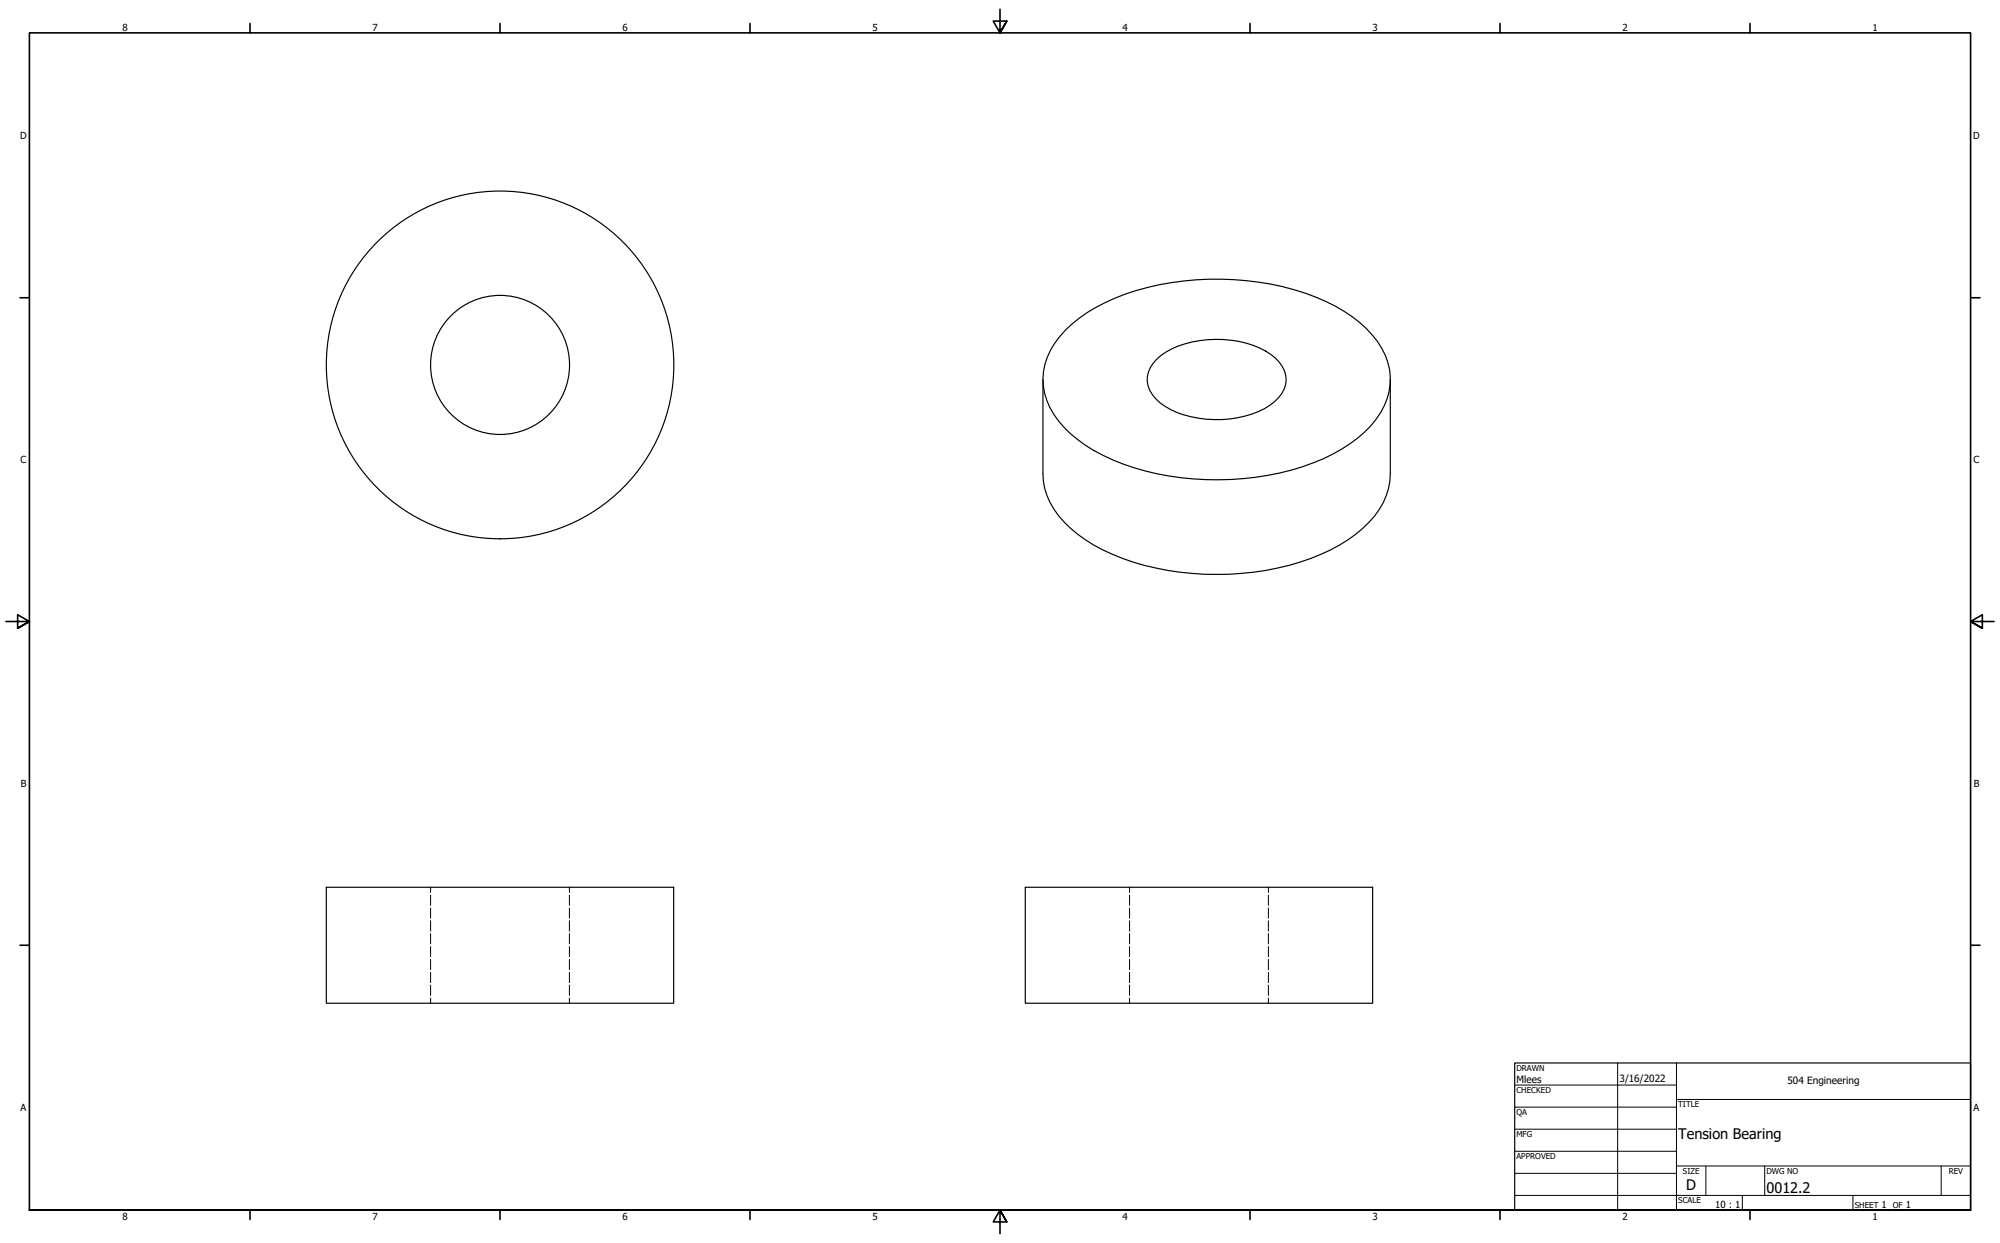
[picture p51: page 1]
Tension Bearing

DRAWN Mlees | 3/16/2022 | 504 Engineering

CHECKED

MFG

APPROVED

SIZE D | DWG NO 0012.2 | REV

SCALE 10 : 1 | | SHEET 1 OF 1

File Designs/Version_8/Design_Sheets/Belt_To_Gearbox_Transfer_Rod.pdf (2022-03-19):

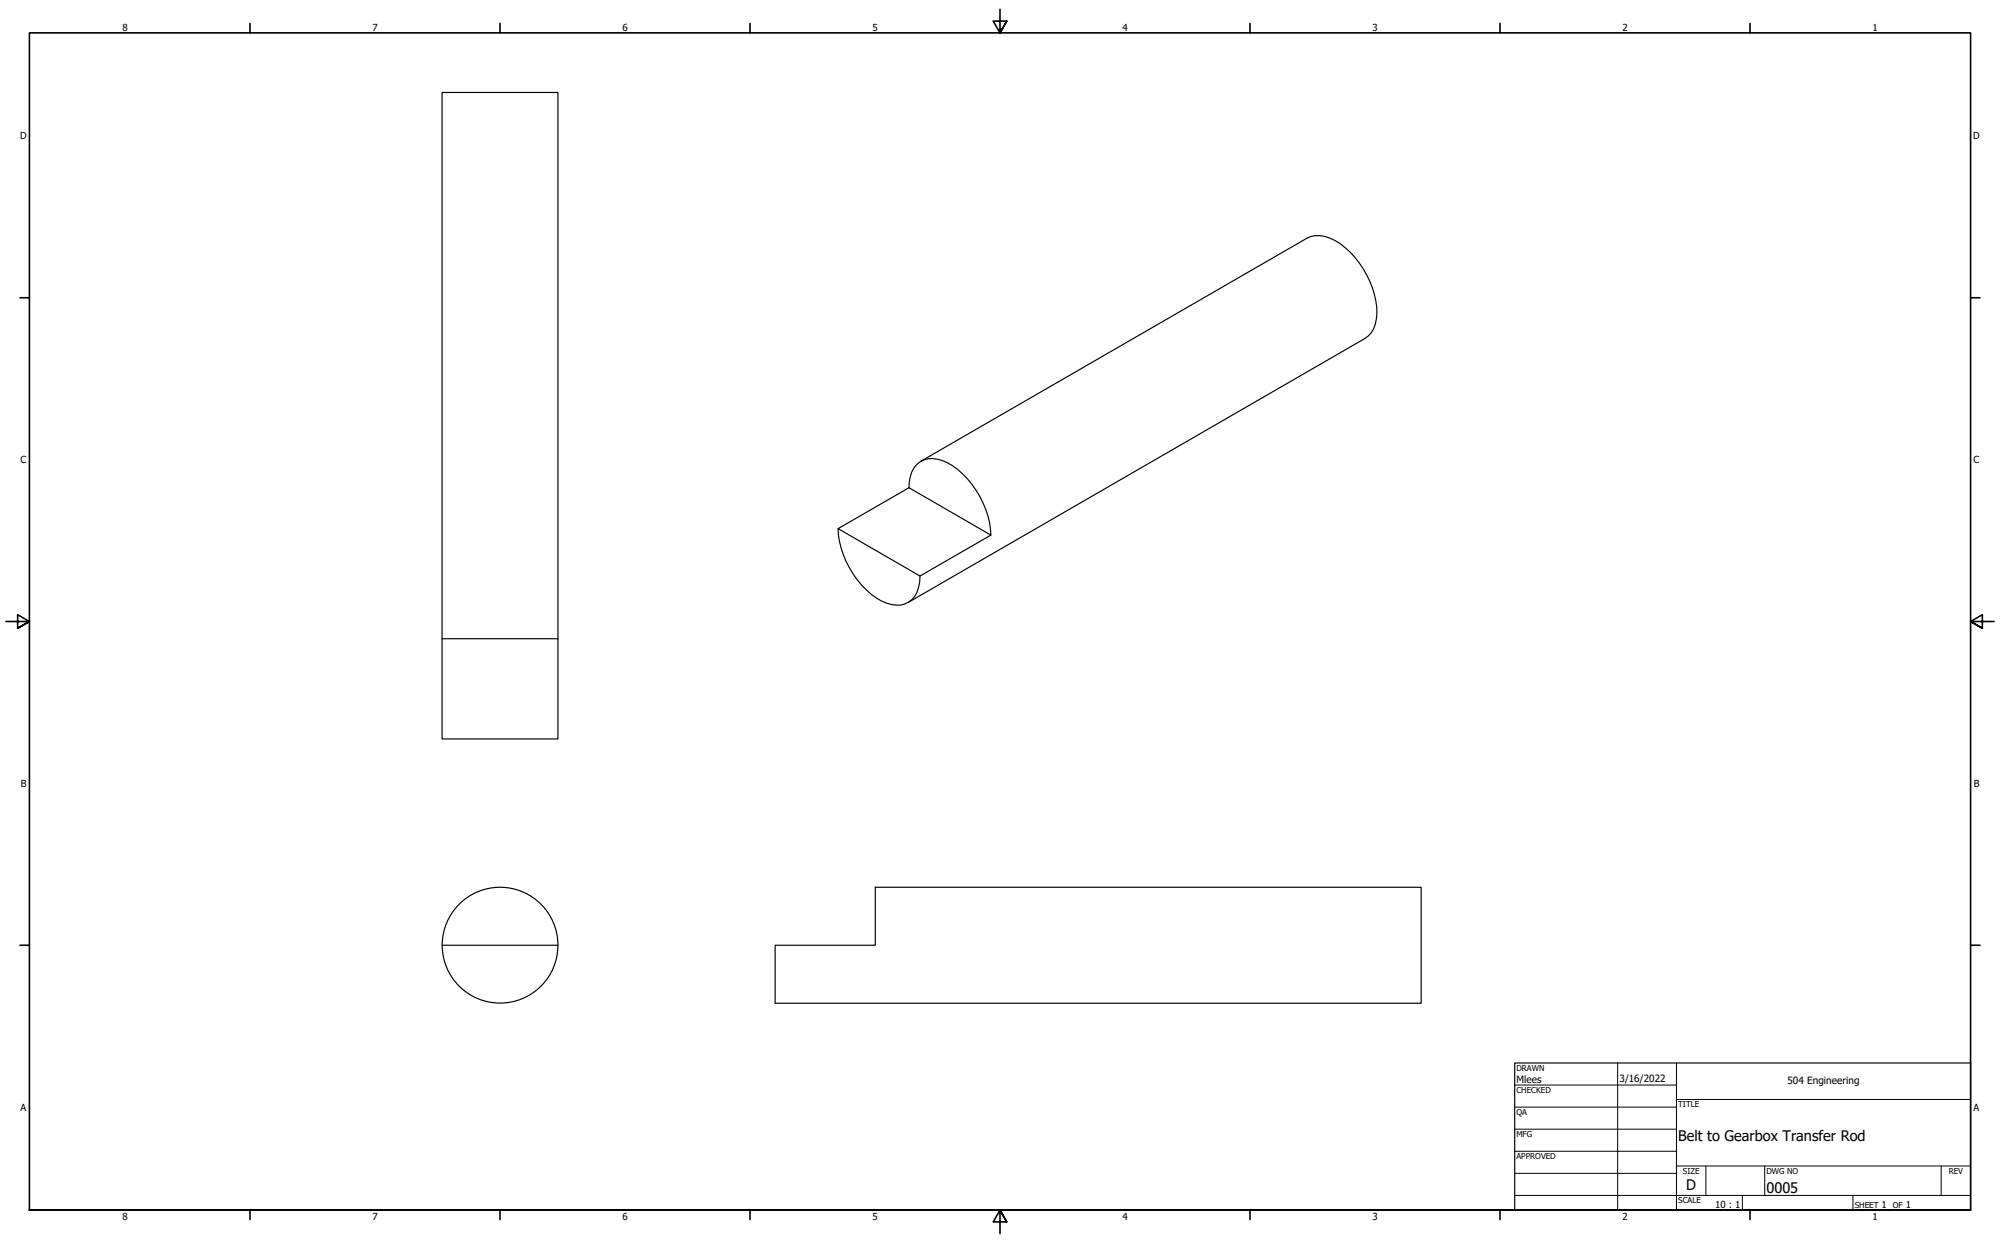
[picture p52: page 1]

DRAWN Mlees | 3/16/2022 | 504 Engineering

CHECKED

MFG

Belt to Gearbox Transfer Rod

APPROVED

SIZE D | DWG NO 0005 | REV

SCALE 10 : 1 | | SHEET 1 OF 1

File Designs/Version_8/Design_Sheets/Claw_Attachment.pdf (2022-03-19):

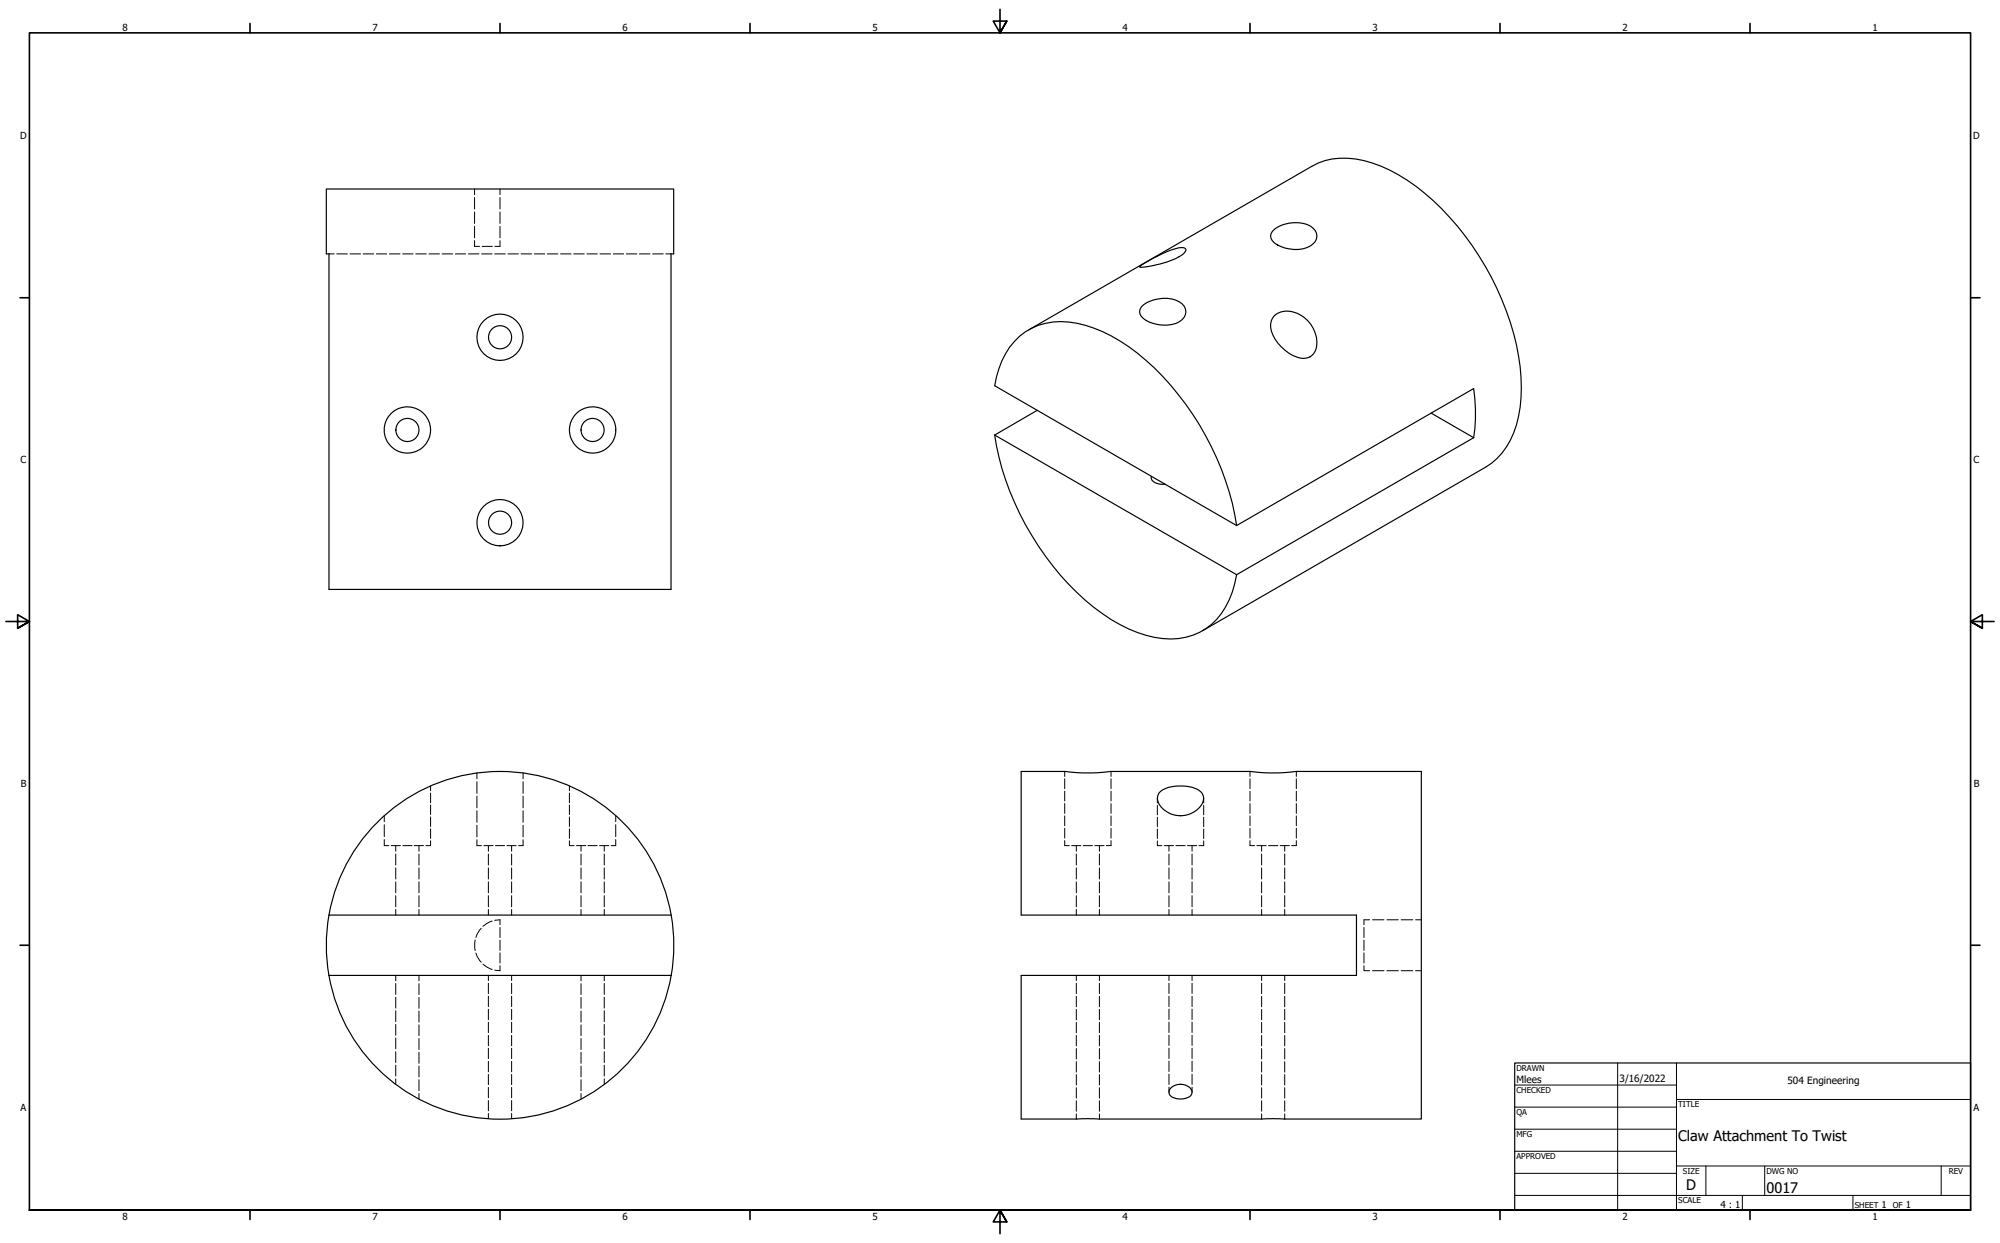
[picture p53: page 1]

DRAWN Mlees | 3/16/2022 | 504 Engineering

CHECKED

MFG

Claw Attachment To Twist

APPROVED

SIZE D | DWG NO 0017 | REV

SCALE 4 : 1 | | SHEET 1 OF 1

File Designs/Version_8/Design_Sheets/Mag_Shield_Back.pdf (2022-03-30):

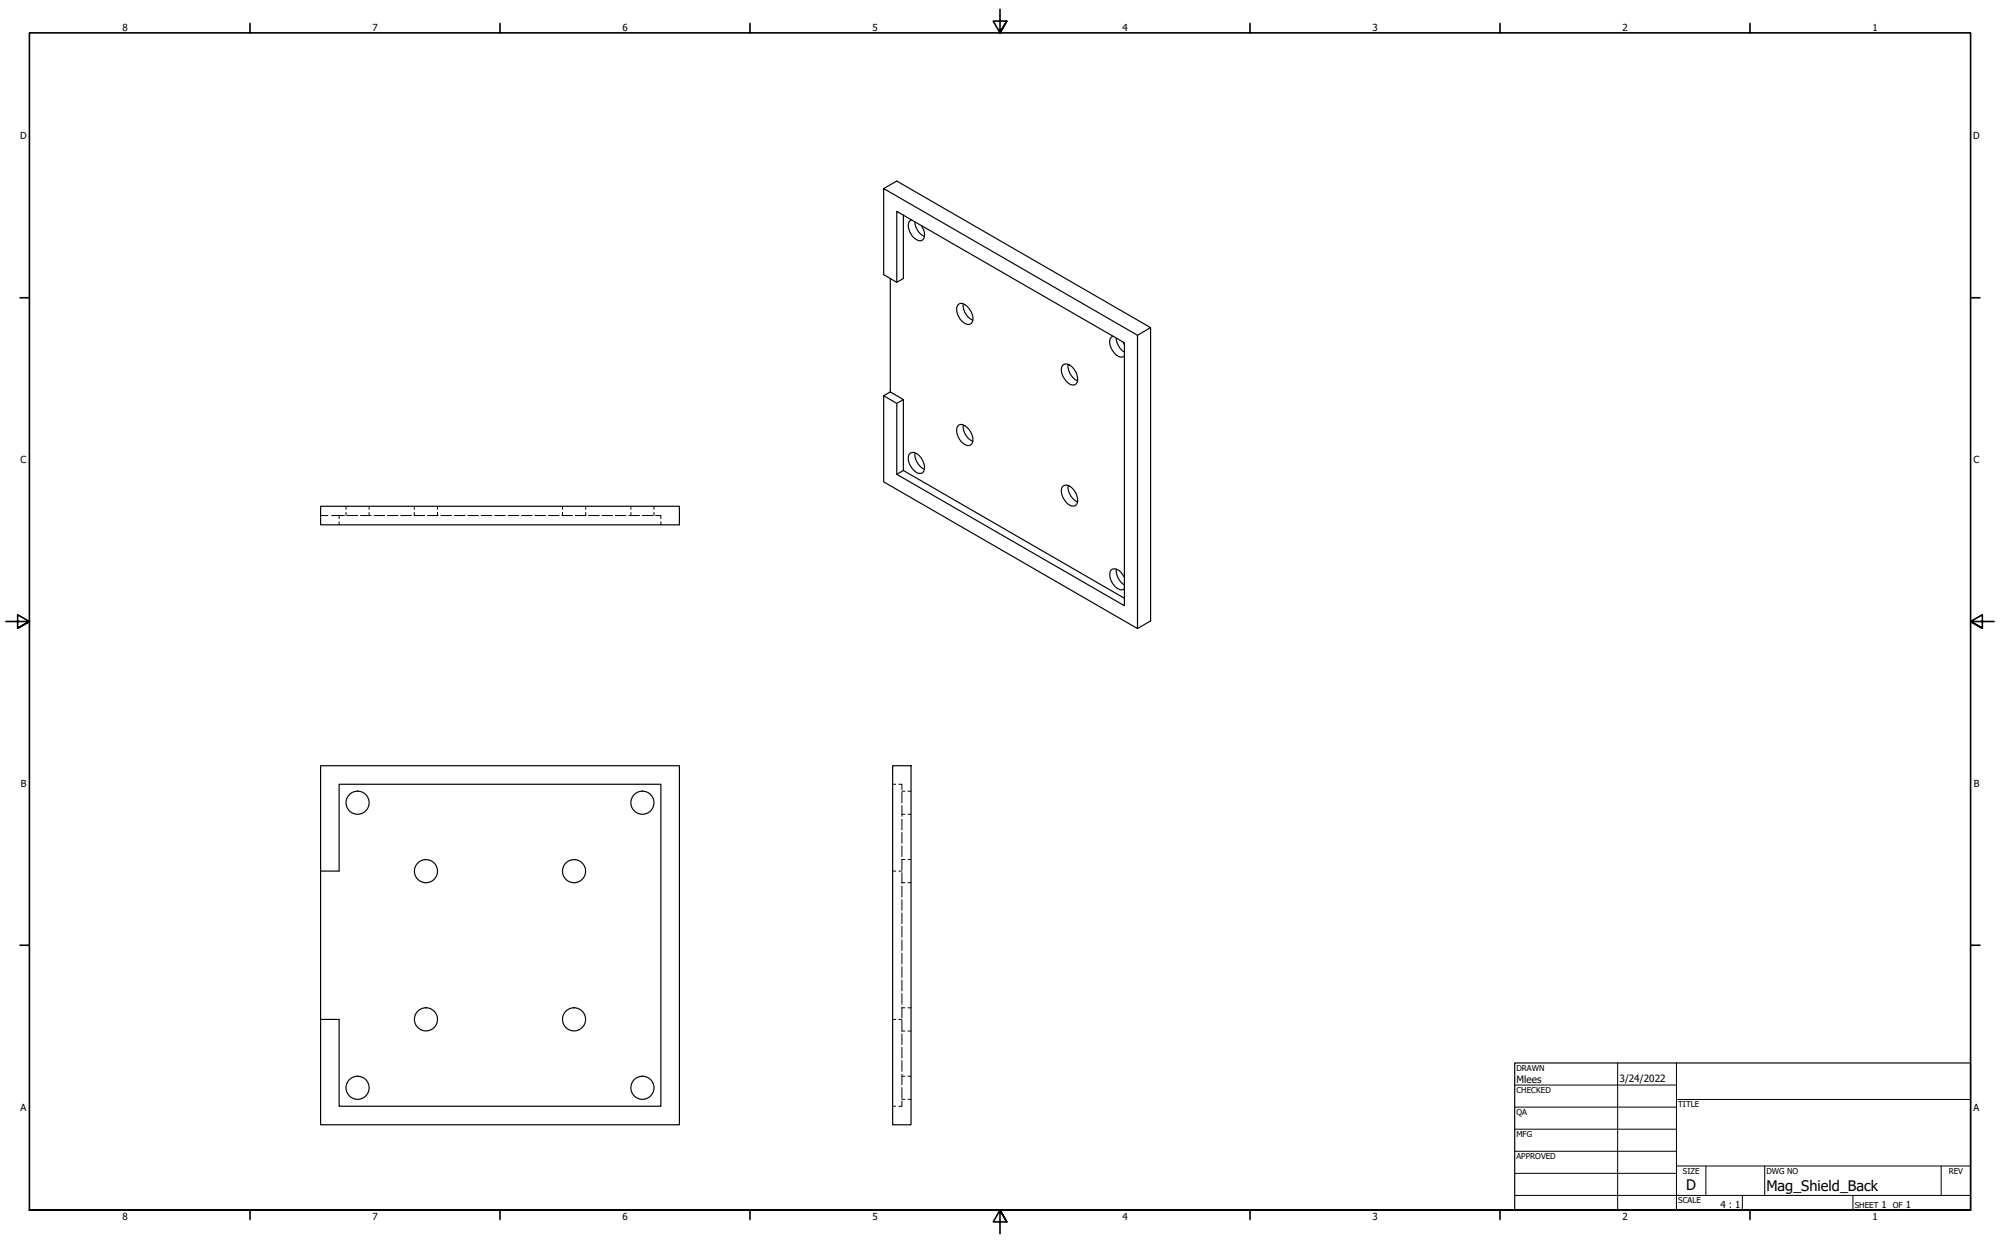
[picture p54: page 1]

DRAWN Mlees | 3/24/2022

CHECKED

MFG

APPROVED

SIZE D | DWG NO Mag_Shield_Back | REV

SCALE 4 : 1 | | SHEET 1 OF 1

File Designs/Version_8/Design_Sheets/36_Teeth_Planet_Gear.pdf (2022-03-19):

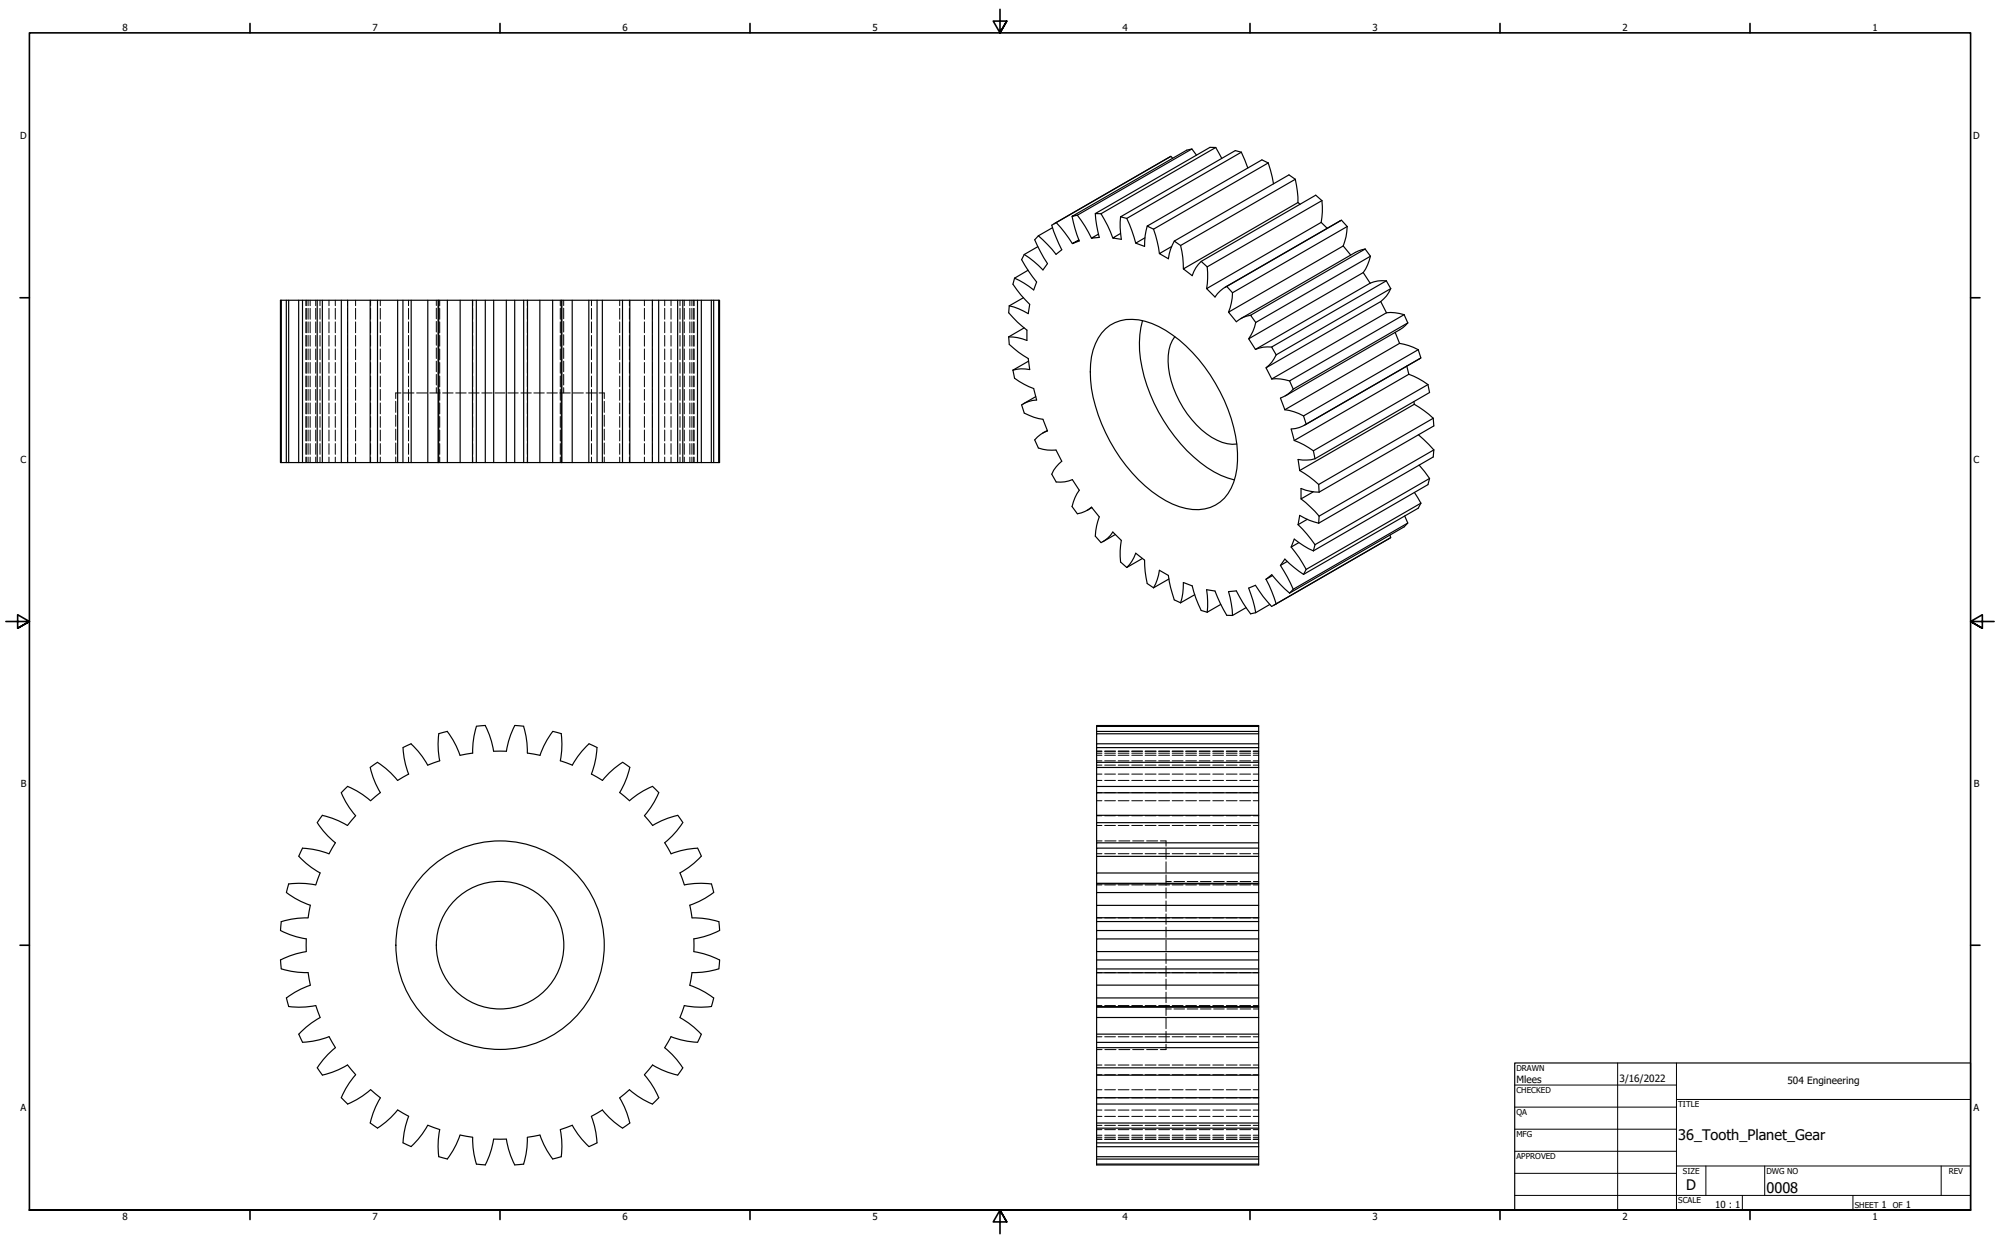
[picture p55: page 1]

DRAWN Mlees | 3/16/2022 | 504 Engineering

CHECKED

MFG

APPROVED

SIZE D | DWG NO 0008 | REV

SCALE 10 : 1 | | SHEET 1 OF 1

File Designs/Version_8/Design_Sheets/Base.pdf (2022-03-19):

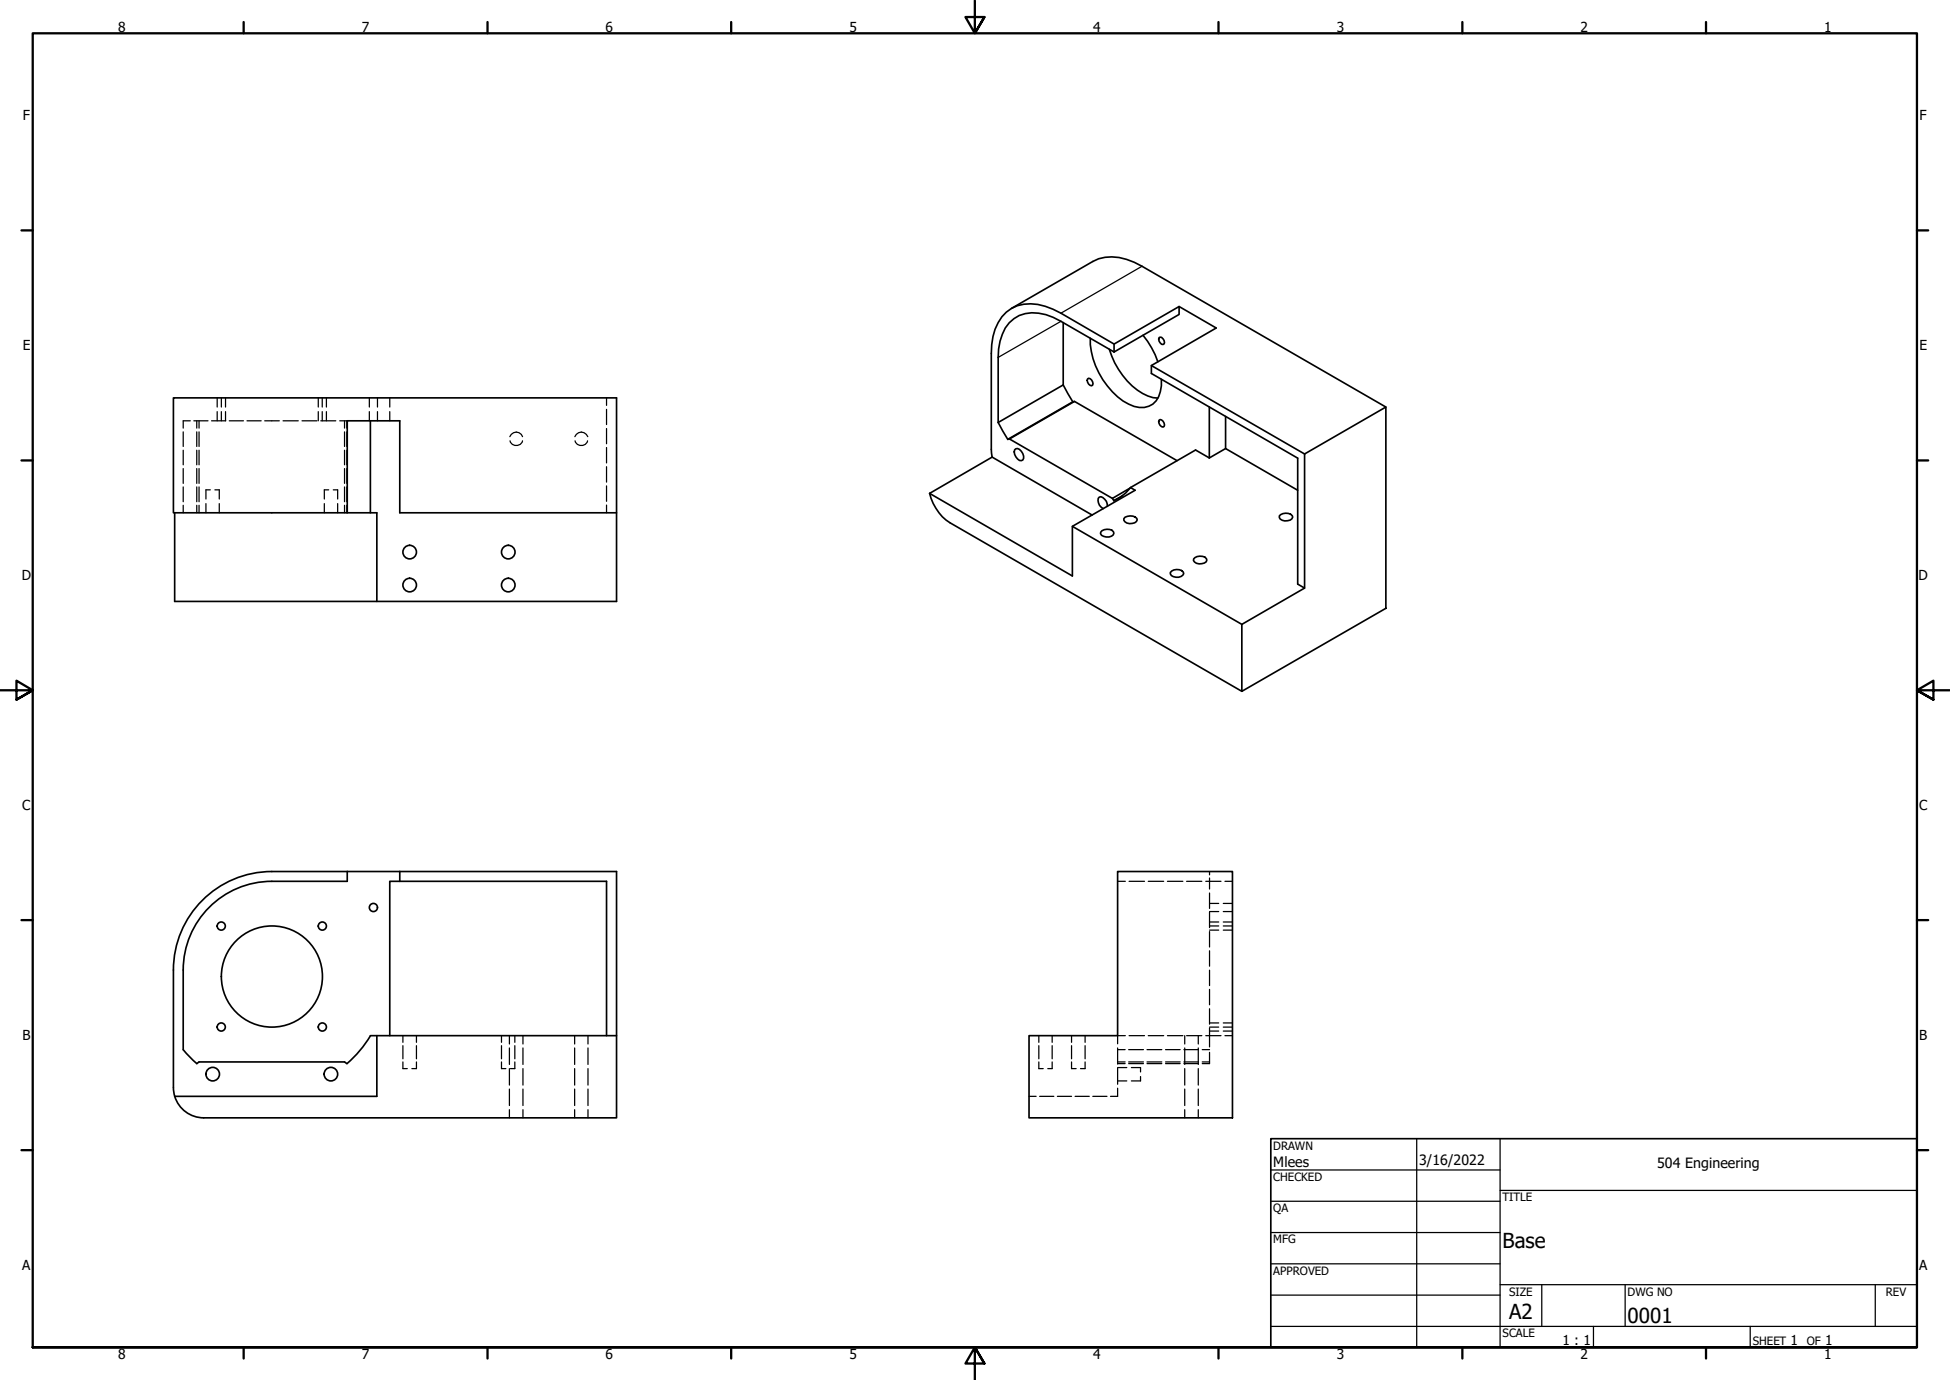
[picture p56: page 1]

DRAWN Mlees | 3/16/2022 | 504 Engineering

CHECKED

MFG

APPROVED

SIZE A2 | DWG NO 0001 | REV

SCALE 1 : 1 | | SHEET 1 OF 1

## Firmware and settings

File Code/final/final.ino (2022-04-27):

#include <AMIS30543.h>
#include <Servo.h>
#include <Wire.h> 
#include <SPI.h>

Servo Cam;
Servo T;
Servo C;

int encoder1 = A7;

// Joint 1 motor pins
const uint8_t j1_dirpin = 6;
const uint8_t j1_steppin = 5;
const uint8_t j1_cs = 7;

// Instantiate joint 1 motor controller
AMIS30543 j1;

// Serial Data variables
int VA = 1500;
int VB = 1500;
int VC = 1500;
int VD = 1500;

void SerialEvent()
{
  Serial.flush();
  char characterBuf[22];  //stores incoming
  int incomingLength = 0; //stores incoming length
  char *token;            //token for converting byte array to string array
  int counterNum = 1;
  //1500,1500,1500,1500\n

  if (Serial.available()) {
    //    Serial.println("1");
    incomingLength = Serial.readBytesUntil('\n', characterBuf, 50);    //calculate length of byte array
    token = strtok(characterBuf, ",");  //convert to string
    VA = atoi(token);
    //    Serial.println(token);
    while (token != NULL) {   //if token doesnt find another comma it goes back to beginning
      token = strtok(NULL, ",");  //changes token to a string def of NULL
      switch (counterNum) {
        case 1:
          VB = atoi(token);
          break;

        case 2:
          VC = atoi(token);
          break;

        case 3:
          VD = atoi(token);
          break;
      }
      counterNum++;
    }
  }
}

void setup() 
{
  Cam.attach(2);
  T.attach(3);
  C.attach(4);
  
  // Starting all the things we need later
  Serial.begin(115200);
  SPI.begin();
  Wire.begin();
  delayMicroseconds(500);

  // initialize the motor controllers
  j1.init(j1_cs);
  delayMicroseconds(500);

  // Write all output pins to low to stop it breaking.
  digitalWrite(j1_steppin, LOW);
  pinMode(j1_steppin, OUTPUT);
  digitalWrite(j1_dirpin, LOW);
  pinMode(j1_dirpin, OUTPUT);
  
  // Set the settings for the stepper motors as follows. 2.4 Amps per motor
  j1.resetSettings();
  j1.setCurrentMilliamps(2070);
  j1.setStepMode(32);
  j1.enableDriver();
}

void loop() 
{
  SerialEvent();
  
  int data = analogRead(encoder1);
  
  int pos1 = map(VA, 1000, 2000, 265, 730);
  
  if (data > pos1 + 2) {
      digitalWrite(j1_dirpin, HIGH);
      for (int i = 0; i < 200; i++) {
        digitalWrite(j1_steppin, HIGH);
        delayMicroseconds(4);
        digitalWrite(j1_steppin, LOW);
        delayMicroseconds(4);
      }
  } else if (data < pos1 - 2) {
      digitalWrite(j1_dirpin, LOW);
      for (int i = 0; i < 200; i++) {
        digitalWrite(j1_steppin, HIGH);
        delayMicroseconds(4);
        digitalWrite(j1_steppin, LOW);
        delayMicroseconds(4);
      }
  } else {
    digitalWrite(j1_dirpin, LOW);
    digitalWrite(j1_steppin, LOW);
  }

  T.writeMicroseconds(VB);
  C.writeMicroseconds(VC);
  Cam.writeMicroseconds(VD);

  Serial.println(String(data) + "," + String(VA) + "," + String(VB) + ","  + String(VC) + ","  + String(VD) + ","  + String(pos1));
}

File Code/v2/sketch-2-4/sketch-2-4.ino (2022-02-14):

// Servo Library
#include <Servo.h>

// Libraries for other stuff
#include <SparkFunLSM6DSO.h>
#include <Wire.h>
#include <SPI.h>
#include <SD.h>
#include <AMIS30543.h>

// SD Card variables
File fd;

const uint_tBUFFER_SIZE = 292;
char filename[] = "recoFile.txt";
char buff[BUFFER_SIZE + 2] = "";
uint8_t index = 0;

const uint8_t chipSelect = 2;
const uint8_t cardDetect = 3;

enum states: uint8_t { NORMAL, E, EO};
uint8_t state = NORMAL;

bool alreadyBegan = false;

/*****************************************/

// Stepper Motors and Servos variables
// Stepper Motor 1
const uint8_t amisDirPin = 4;
const uint8_t amisStepPin = 5;
const uint8_t amisSlaveSelect = 6;

AMIS30543 stepper;
AMIS30543 stepper2;

// Stepper Motor 2
const uint8_t amisDirPin2 = 7;
const uint8_t amisStepPin2 = 8;
const uint8_t amisSlaveSelect2 = 9;

/*****************************************/

// Accelerometer variables
int16_t AcX, AcY, AcZ, AcX1, AcY1, AcZ1;
double x, y, z, x1, y1, z1;
double AcX_o, AcY_o, AcZ_o, AcX1_o, AcY1_o, AcZ1_o;

/*****************************************/

// Servo variables
Servo S1;
Servo S2;

/*****************************************/

// Serial data variables
int VA = 1500;
int VB = 1500;
int VC = 1500;
int VD = 1500;

/*****************************************/

void step( uint8_t pin )
{
  digitalWrite( pin, HIGH );
  delayMicroseconds( 3 );
  digitalWrite( pin, LOW );
  delayMicroseconds( 3 );
  delayMicroseconds( 2000 );
}

void setDirection( uint8_t pin, bool dir )
{
  delayMicroseconds( 1 );
  digitalWrite( pin, dir );
  delayMicroseconds( 1 );
}

void SerialEvent()
{
  Serial.flush();
  char characterBuf[22];  //stores incoming
  int incomingLength = 0; //stores incoming length
  char *token;            //token for converting byte array to string array
  int counterNum = 1;

  if (Serial.available()) {
    //    Serial.println("1");
    incomingLength = Serial.readBytesUntil('\n', characterBuf, 50);    //calculate length of byte array
    token = strtok(characterBuf, ",");  //convert to string
    VA = atoi(token);
    //    Serial.println(token);
    while (token != NULL) {   //if token doesnt find another comma it goes back to beginning

      token = strtok(NULL, ",");  //changes token to a string def of NULL
      //      Serial.println(token);

      switch (counterNum) {
        case 1:
          VB = atoi(token);
          break;

        case 2:
          VC = atoi(token);
          break;

        case 3:
          VD = atoi(token);
          break;
      }
      counterNum++;
    }
  }
}

void initializeCard( void )
{
  Serial.print( F("Initializing SD card...") );

  // Is there even a card?
  if ( !digitalRead(cardDetect) )
  {
    Serial.println(F( "No card detected. Waiting for card.") );
    while (!digitalRead(cardDetect));
    delay(250); // 'Debounce insertion'
  }

  // Card seems to exist.  begin() returns failure
  // even if it worked if it's not the first call.
  if (!SD.begin(chipSelect) && !alreadyBegan)  // begin uses half-speed...
  {
    Serial.println(F("Initialization failed!"));
    initializeCard(); // Possible infinite retry loop is as valid as anything
  }
  else
  {
    alreadyBegan = true;
  }
  Serial.println(F("Initialization done."));

  Serial.print(fileName);
  if (SD.exists(fileName))
  {
    Serial.println(F(" exists."));
  }
  else
  {
    Serial.println(F(" doesn't exist. Creating."));
  }

  Serial.print("Opening file: ");
  Serial.println(fileName);

  Serial.println(F("Good to go."));
}

void flushBuffer( String s )
{
  fd = SD.open( fileName, FILE_WRITE );
  fd.println( s );
  fd.close( );
}

void setup( ) 
{
    Serial.begin( 250000 );
    delay( 500 ); 

    Wire.begin( );
    delay( 10 );

    if ( stepper.begin( 0x6A ) ) {
        Serial.println( "Ready." );
    } else {
        Serial.println( "Could not connect to IMU." );
        Serial.println( "Freezing" );
    }
    if ( stepper.initialize( BASIC_SETTINGS ) ) {
        Serial.println( "Loaded Settings." );
    }

    if ( stepper2.begin( 0x6B ) ) {
        Serial.println( "Ready." );
    } else {
        Serial.println( "Could not connect to IMU." );
        Serial.println( "Freezing" );
    }
    if ( stepper2.initialize( BASIC_SETTINGS ) ) {
        Serial.println( "Loaded Settings." );
    }

    S1.attach( 7 );
    S2.attach( 6 );

    pinMode( step1, OUTPUT );
    pinMode( step2, OUTPUT );
    pinMode( dir1, OUTPUT );
    pinMode( dir2, OUTPUT );

    S1.writeMicroseconds( 1500 );
    S2.writeMicroseconds( 1500 );

    pinMode(cardDetect, INPUT);
    initializeCard();
}

void loop( ) 
{

}

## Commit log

2022-01-19 Current Status
    This contains the current files for the Robotic arm along with various different drive trains for the stepper motors for each tilt joint. Current version is Assembly_Trial_3
    [24_Teeth_Sun_Gear.step.ipt, 24_Teeth_Sun_Gear.step.stl, 24_Teeth_Sun_Gear.stl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]
2022-01-20 started the design of the tilt bracket
    [Assembly_Trial_3.0002.iam, Assembly_Trial_3.0003.iam, Assembly_Trial_3.iam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]
2022-01-21 Created the support structures and the tilt bracket
    [4668K221_Permanently Lubricated Stainless Steel Ball Bearing.SLDPRT, 604-2R2_Bearing4668K221_Permanently Lubricated Stainless Steel Ball Bearing.ipt, 95836A221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]
2022-01-21 saved the files i forgot to save
    [95836A221_Black-Oxide 18-8 Stainless Steel Pan Head Phillips Screws.ipt, 96_Teeth_Gear.step.0002.ipt, 96_Teeth_Gear.step.0003.ipt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]
2022-01-21 finished the first tilt prototype
    [90666A106_Super-Corrosion-Resistant 316 Stainless Steel Socket Head Screw.SLDPRT, 90666A106_Super-Corrosion-Resistant 316 Stainless Steel Socket Head Screw.ipt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]
2022-01-22 Finished the design for the first tilt
    printing the parts now for testing
    [24_Teeth_Sun_Gear.step.stl, 36_Teeth_Planet_Gear.step.stl, 96_Teeth_Gear.step.stl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]
2022-01-23 lots of additions
    [Assembly_Trial_3.0011.iam, Assembly_Trial_3.0013.iam, Assembly_Trial_3.iam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]
2022-01-31 new version number
    [24_Teeth_Sun_Gear.0002.ipt, 24_Teeth_Sun_Gear.ipt, 24_Teeth_Sun_Gear.step.ipt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]
2022-02-14 two new versions
    [24_Teeth_Sun_Gear.0003.ipt, 24_Teeth_Sun_Gear.ipt, 24_Teeth_Sun_Gear.step.ipt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]
2022-02-18 creation of new gcodes
    [Assembly2.0001.iam, Assembly2.0002.iam, Assembly2.iam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]
2022-03-02 revisions after testing 3d printed models
    [24_Teeth_Sun_Gear.0003.ipt, 24_Teeth_Sun_Gear.0006.ipt, 24_Teeth_Sun_Gear.ipt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]
2022-03-07 new version didnt make new folder thou
    [Base_Mount.ipt, Base_Mount.stl, Combined_Gear_Box_Modified_3.0020.ipt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]
2022-03-11 magnetic encoders
    moving towards magnetic encoders, might work better than the accelerometers. Would need to use the pico though.
    [Full_Design.0007.iam, Full_Design.0008.iam, Full_Design.iam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]
2022-03-13 Explorer Team wanted only one joint
    [24_Teeth_Sun_Gear.0006.ipt, 24_Teeth_Sun_Gear.ipt, 24_Teeth_Sun_Gear.step.ipt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]
2022-03-19 creation of documentation started
    [24_Teeth_Sun_Gear.0002.dwg, 24_Teeth_Sun_Gear.dwg, 36_Teeth_Planet_Gear.0001.dwg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]
2022-03-21 Lots of documentation changes
    [2349K743_Permanently Lubricated Ball Bearing.SLDPRT, 4668K127_Permanently Lubricated Stainless Steel Ball Bearing.SLDPRT, 4668K127_Permanently Lubricated Stain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]
2022-04-27 they asked me to make more stuff
    [Camera_Mount.0002.ipt, Camera_Mount.ipt, Camera_Mount.stl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]
